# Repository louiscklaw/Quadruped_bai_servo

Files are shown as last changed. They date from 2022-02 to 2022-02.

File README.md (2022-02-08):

# Quadruped_bai_servo v1
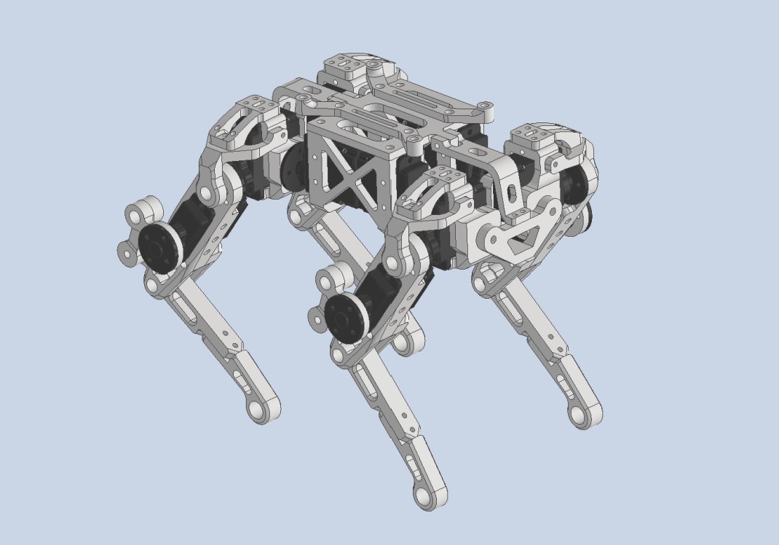
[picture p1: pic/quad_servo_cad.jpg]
quad_servo_cad


A low cost 12DOF quadruped, actuated by hobby servos. Notice that this is an early version developed back in 2019. If you're looking for a high performance desktop quad, check out the ongoing [Quadruped bai tiny](https://github.com/psrobotics/Quadruped_bai_tiny)

This repository contains the models, BOM, electronic, simulate, as well as the source code of the project.

## Videos

[Balancing](https://www.youtube.com/watch?v=fsc0w1NeIVk)

[Walking](https://youtu.be/FCRvykWv6ok)

## Hardware

Required parts are listed below. For all printed parts, the recommended printing infill is 70%. Set up proper printing direction and support based on your printer type.

| Part Name | Quantity | Link | Info |
| --- | --- | --- | --- |
| leg_tip | 2 | [STL file](hardware/stl) | Printed part |
| leg_tip_MIR | 2 | / | / |
| leg_2 | 2 | / | / |
| leg_2_MIR | 2 | / | / |
| leg_link_1 | 2 | / | / |
| leg_link_1_MIR | 2 | / | / |
| leg_link-1 | 2 | / | / |
| leg_link-1_MIR | 2 | / | / |
| leg_1 | 2 | / | / |
| leg_1_MIR | 2 | / | / |
| leg_1_2 | 2 | / | / |
| leg_1_2_MIR | 2 | / | / |
| servo_holder_1 | 2 | / | / |
| servo_holder_1_MIR | 2 | / | / |
| hip_joint_holder_1 | 2 | / | / |
| hip_joint_holder_1_MIR | 2 | / | / |
| hip_holder_2 | 2 | / | / |
| hip_holder_2_MIR | 2 | / | / |
| joint_ab_holder | 2 | / | / |
| body_bridge | 2 | / | / |
| body_frame_2 | 1 | / | / |
| body_frame_1 | 1 | / | / |
| pcb_holder | 2 | / | / |
| M3*8 | ~20 | / | Screw |
| M3*12 | ~30 | / | / |
| M3*16 | ~20 | / | / |
| M2*8 | ~50 | / | / |
| M2*15 | ~50 | / | / |
| M2*20 | ~20 | / | / |
| M2*26 | ~20 | / | / |
| SF-1 0305 Self Lubricating Composite Bearing Bushing Sleeve | ~25 | [ebay](https://www.ebay.com/itm/141882850401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) | For rotation joints |
| EMAX ES08A II Servo | 12 | [EMAX](https://emaxmodel.com/products/emax-es08a-ii-mini-plastic-gear-analog-servo-1-8kg-sec-for-rc-models-robot) | Actuator |

After printing your parts, insert the bearing at all 5mm holes locates around rotations joints. Then fasten  parts with M3 screws. Remember to check the rotation friction, make sure all joints can rotates freely with the servo installed. 

### Servo selection

The performance of actuators is of fundamental importance for legged robots. Even when we're building a small one. Ideal actuators for this design should be highly back-drivable, have high power density, and be torque-controllable. However, most off-the-shelf servos have nothing to do with these features. There are some high voltage brushless servos (with magnetic encoders for feedback) with relatively good performance, but they're extremely costive at this size. If you have enough budget, why not build a brushless one? Considering that you'll need 12 servos for the assembly, my suggestion is just to go for the budget choice. The EMAX ES08A (metal gear version) works fine for my build. The nylon gear version is also acceptable, but they can easily be damaged under impact.

### Body assembly

The robot consists 4 legs and a body frame. Assembly 2 legs first.

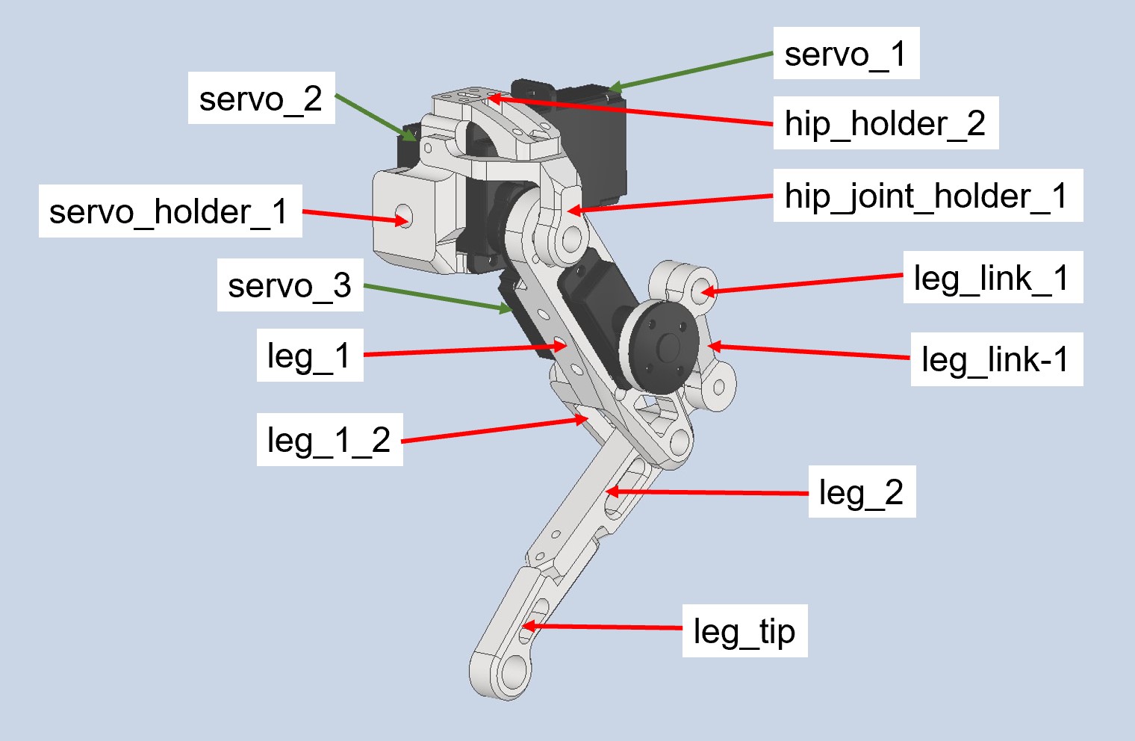
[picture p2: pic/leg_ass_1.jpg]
leg_ass_1


Assembly another 2 mirrored legs. Then link all legs to the body frame.

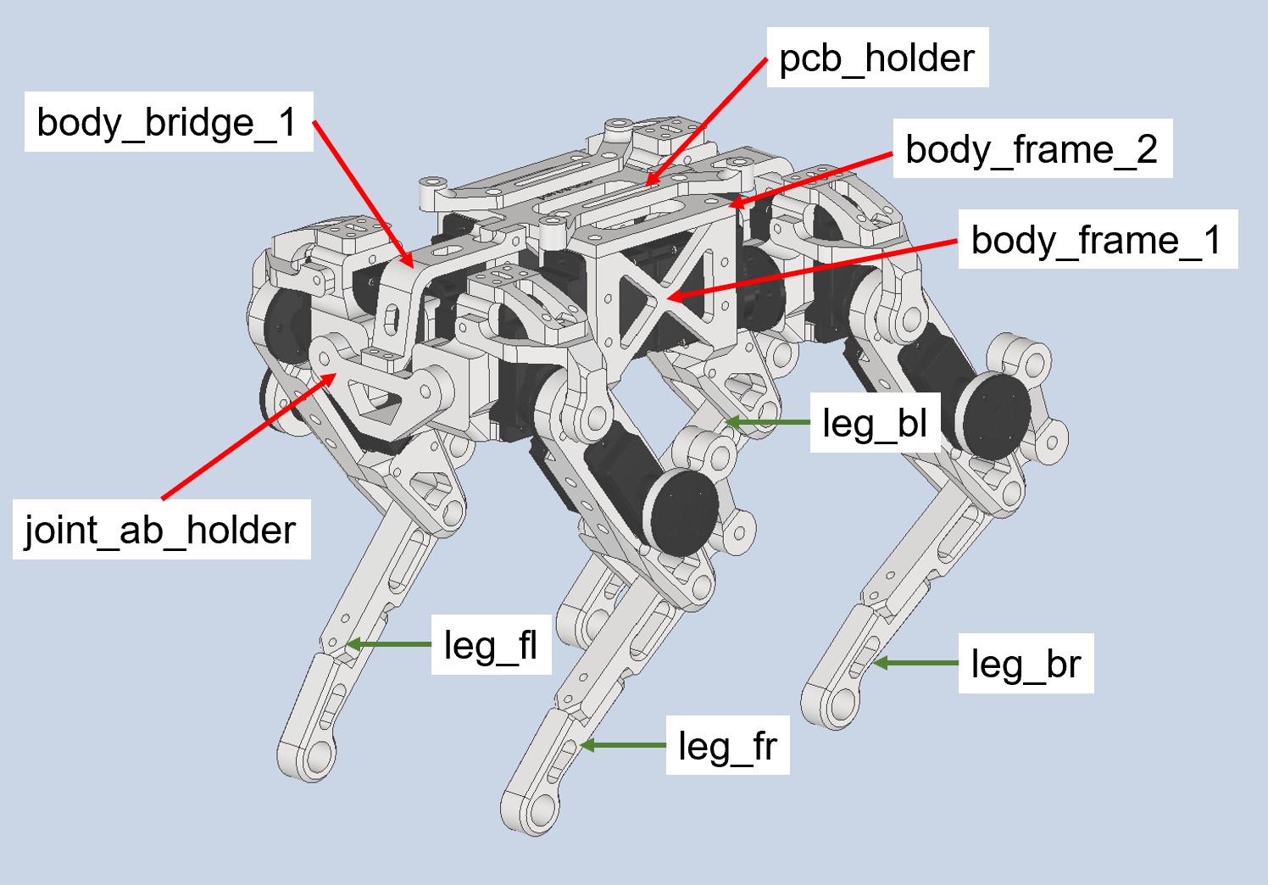
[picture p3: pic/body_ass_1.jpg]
body_ass_1


### Feet Sensor (optional)

Additional feet sensors can detect whether foot have touched the ground. This can be helpful when changing the state machine from 'swing state' to 'stance state'. The foot of Quadruped bai servo is switchable. If you decided to add feet sensors, some additional configurations are needed for the firmware (would be detailly explained later). 

Feet sensors are built around micro switches,  which detect impact from specific directions. As for the result, this design didn't work that well. A good feet sensor solution should be able to detect impacts from all directions, with low latency and clear output. [Open Dynamic Robot Initiative](https://open-dynamic-robot-initiative.github.io/) has presented an elegant solution with infrared sensor. Take that as a reference, the ongoing Quadruped bai tiny will come with better feet sensors. Assembly the feet sensor as this pic shown. (Remember to print mirrored parts for right-side legs)

Only 3 printed parts are needed to assembly the feet sensor, check [STL file](hardware/stl/feet_sensor) here.

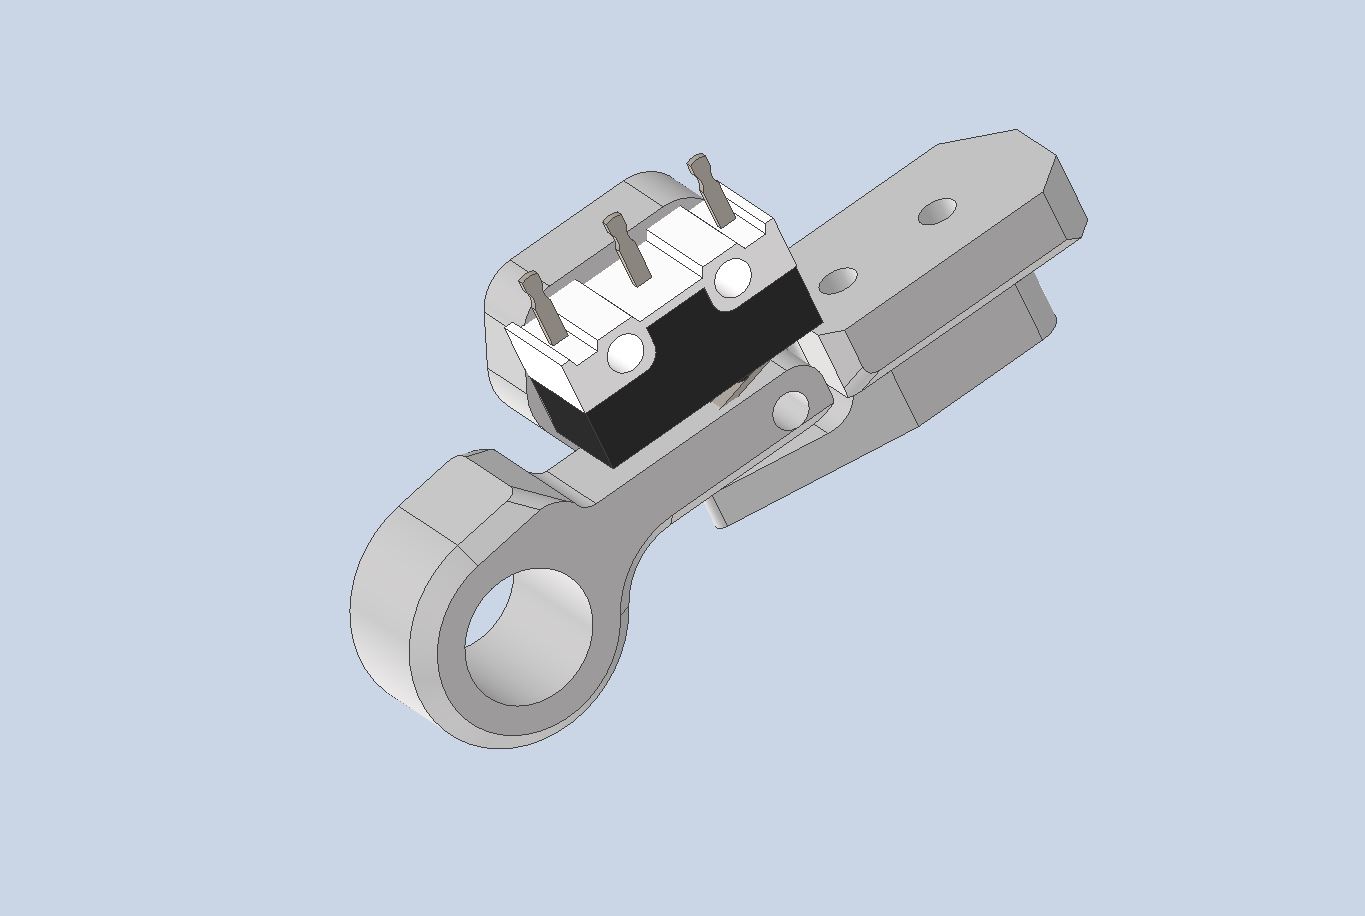
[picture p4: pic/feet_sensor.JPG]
feet_sensor


In order to increase the friction between feet and ground, additional high-friction coating is vital. I used some glued silicone sheet on the feet tip. You can also design your feet tip and print it with high-friction material.

### Servo Calibration

Most servos have a limited motion range,  make sure the servo's motion range covers leg linkage's joint limit shown in the following pics.  Also, pre-calibrate in this step by applying an initial PWM signal to servos before installing (eg. 0°). This enables all servos to have the same PWM-joint angle mapping. You can then fine-tuning them in the firmware.

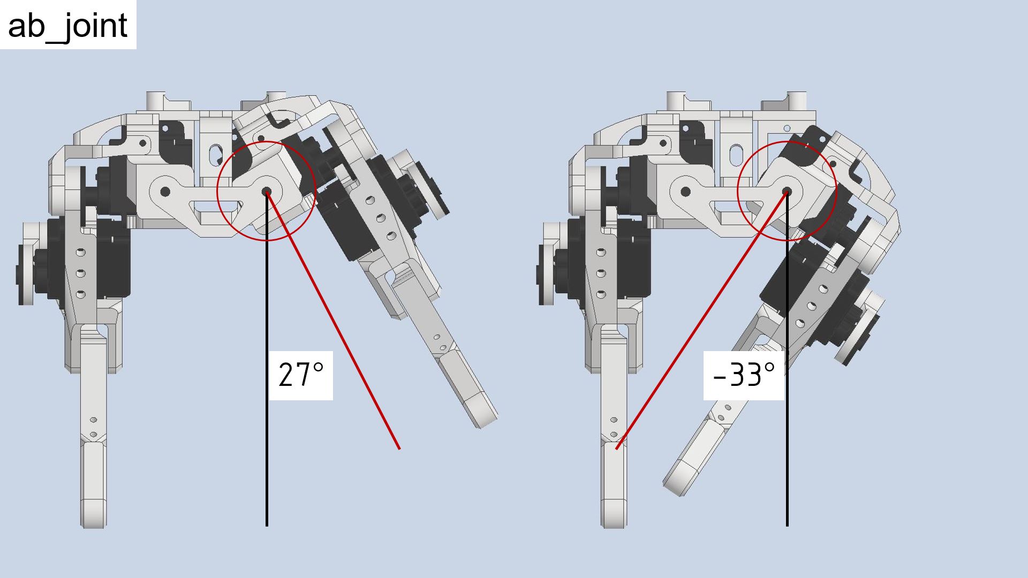
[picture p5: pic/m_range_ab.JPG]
ab joint


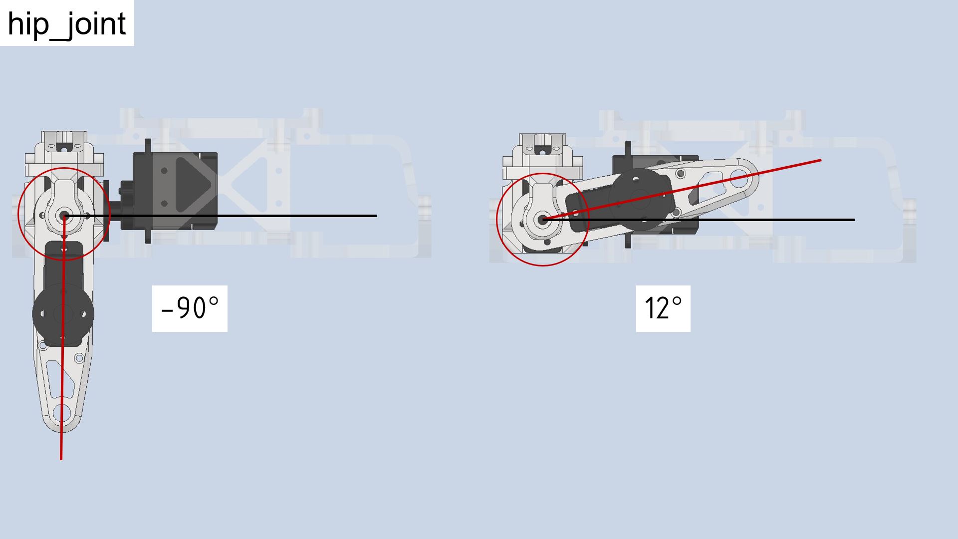
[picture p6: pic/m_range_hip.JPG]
hip joint


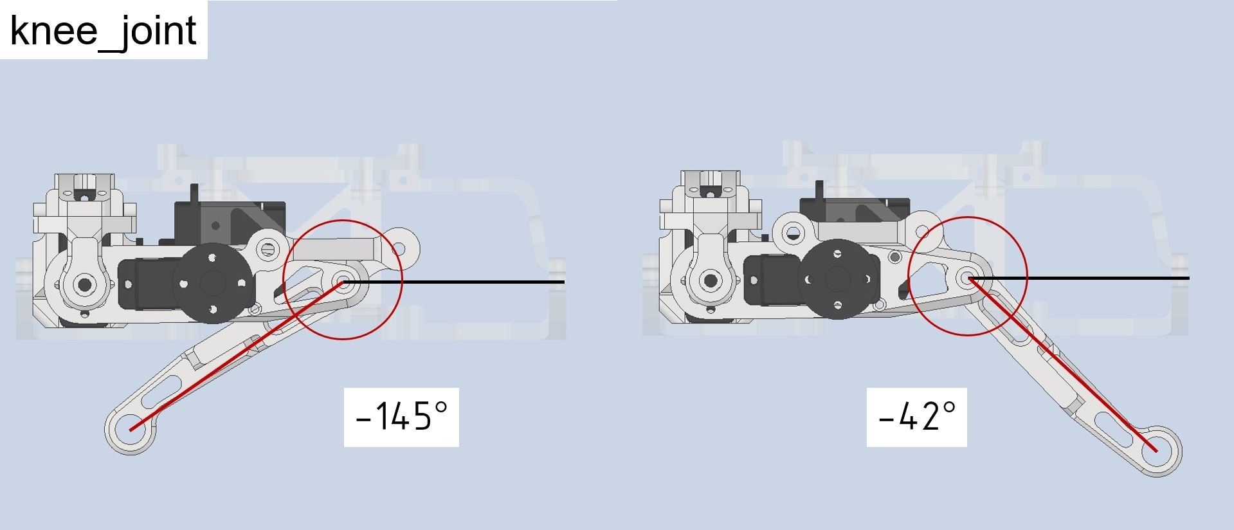
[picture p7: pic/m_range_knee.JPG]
knee joint


## Electronic

The controller board assembly includes servo controller, IMU, and dc-dc converter module. With an additional serial port, you can connect robot to a wireless or Bluetooth module that enables wireless control. Built around ATmega328P, the microcontroller's performance, IO is just not enough for such application. I encourage you take this schematic as a reference and switch to a high performance 32-bit microcontroller (something like STM32H7, ESP32). If you're more comfortable with AVR Arduino boards, use this design directly and it'll work.

[PCBs](electronic/) are designed with [EAGLE](https://www.autodesk.com/products/eagle/free-download). Exported Gerber file is uploaded too. If you don't want to order the PCB, you can also make it using off-the-shelf components (Arduino nano, MPU 6050, dc-dc converter, etc).

### Controller board pin assignment

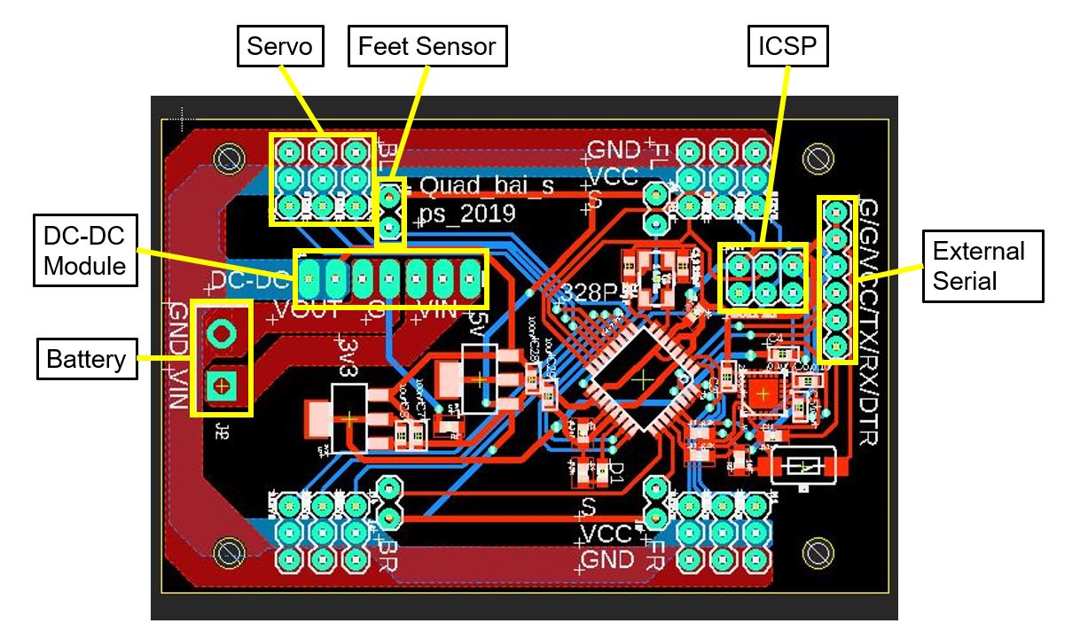
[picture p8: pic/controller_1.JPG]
ctr_brd


Use ICSP to upload firmware and debug with the external serial port. The hardware IIC pins(A4,A5) are occupied by IMU (MPU6050 is also an 'old chip', you can replace with something like BNO080). 

### DC-DC converter

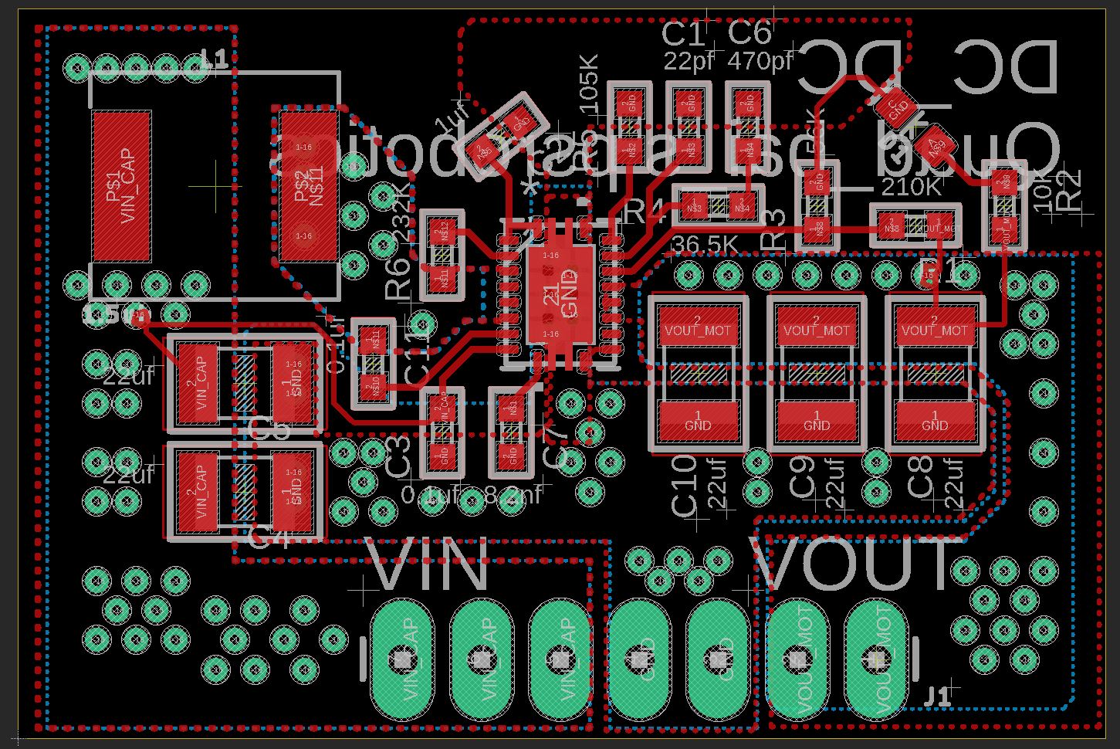
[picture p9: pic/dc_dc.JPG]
dc_dc


Integrated boost converter to power servos. Pre-configured output voltage is 5.5V, you can change by [replacing](https://www.ti.com/lit/ds/symlink/tps61088.pdf?ts=1644121246192#:~:text=The%20TPS61088%20is%20a%20high,size%20solution%20in%20portable%20systems.&text=The%20device%20has%2010%2DA,voltage%20up%20to%2012.6%20V.) the feedback resistor. Plug this module to the DC-DC slot on controller board.

### Battery

Single-cell lithium batteries with high current output capability(>10A) are preferred. This project uses 18650, 18350 batteries. The [battery shelf](hardware/step) can be printed and mounted under the robot frame.

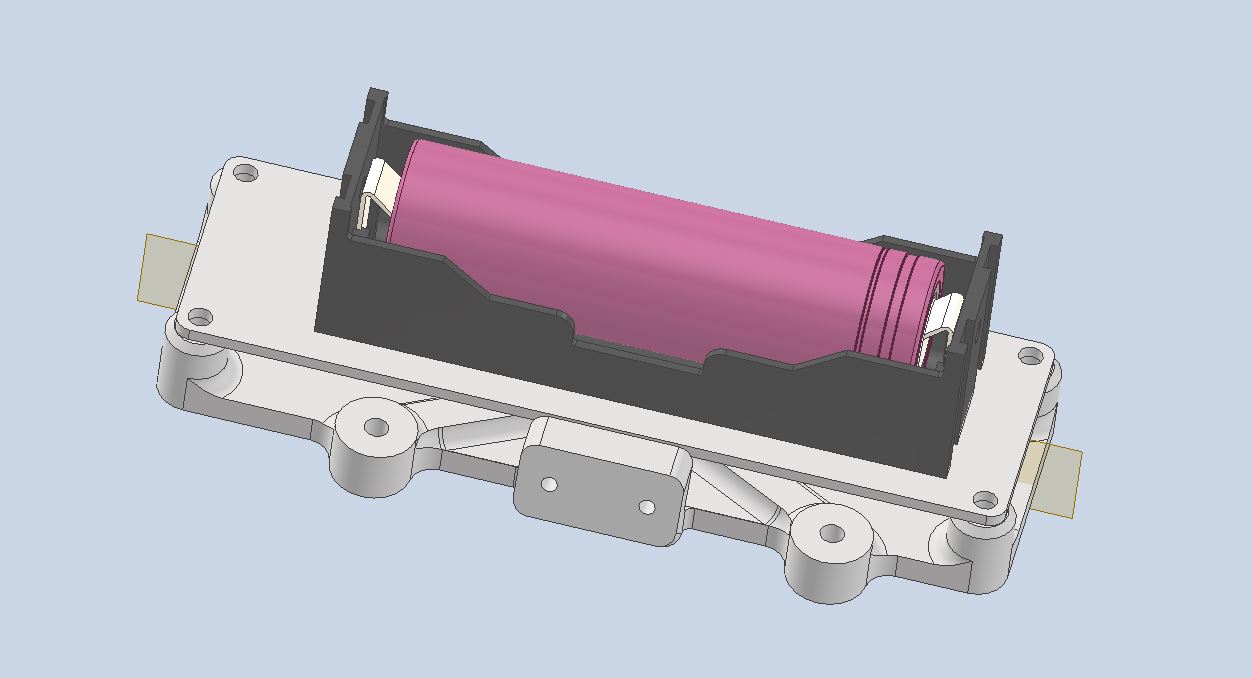
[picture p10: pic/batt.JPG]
batt


## Simulate

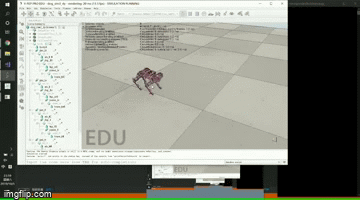
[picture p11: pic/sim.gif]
simulate


Simplified model in [v-rep](https://www.coppeliarobotics.com/). You can use remote API to develop your simulation.

### Coordinate system in the simulation

TODO, write this docu when I'm free.

## Firmware

A simplified controller is implemented to generate trot pattern for walking. Here, I applied a state machine to easily synchronize a set of open foot trajectories (with feet sensor). The IMU unit is used to adjust body roll&pitch during the stance phase. Notice that this robot is only controlled on the kinematic level, don't expect it to resist external impacts during walking process.

## License

Under BSD-3-Clause license, COME WITH NO WARRANTIES, BUILD AT YOUR RISK.

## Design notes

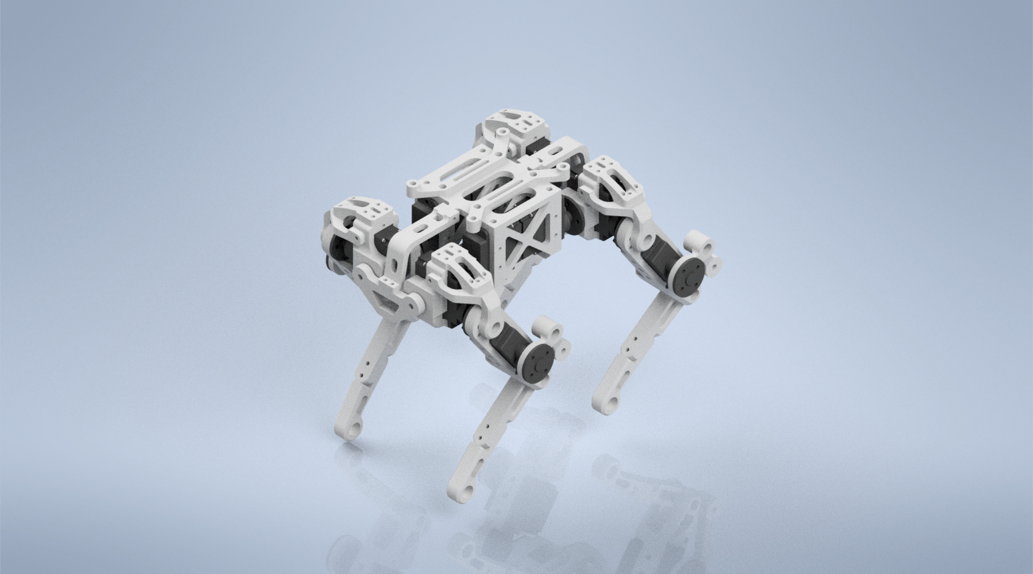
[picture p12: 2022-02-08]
docs/index.png

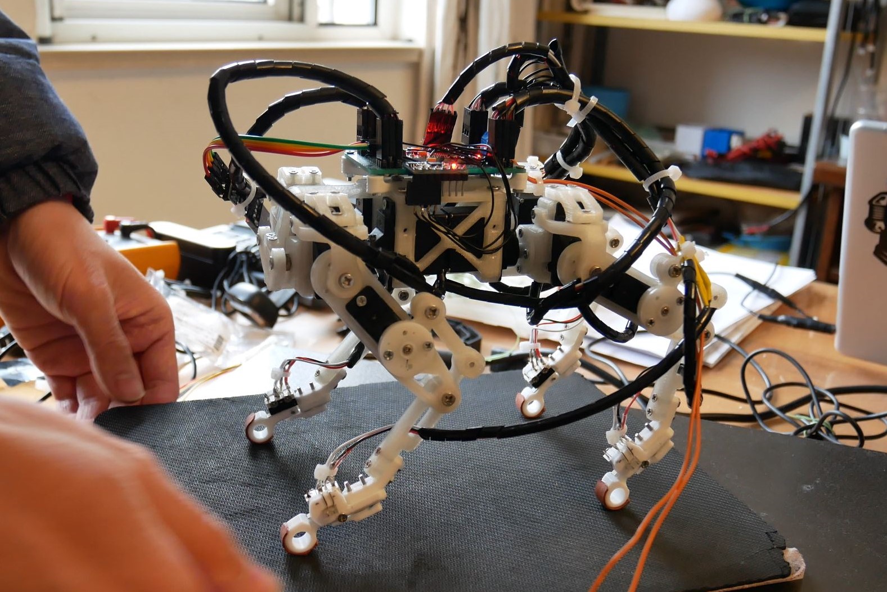
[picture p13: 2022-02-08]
pic/quad_servo.jpg

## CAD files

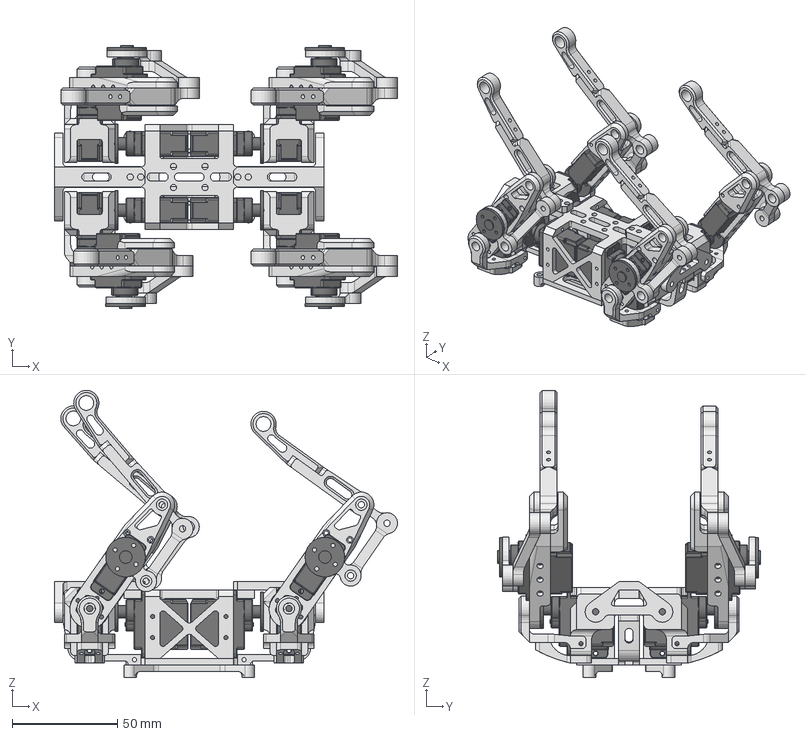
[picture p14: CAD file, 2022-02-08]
hardware/step/quadruped_bai_servo_assembly.stp
162.6 x 124.6 x 136.2 mm
Emax ES08A x 6
leg_1 x 2
leg_2 x 2
leg_1_2 x 2
leg_link_1 x 2
leg_link-1 x 2
leg_tip x 2
servo_holder_1
hip_joint_holder_1 x 2
hip_holder_2 x 2
servo_holder_1_MIR
Emax ES08A_MIR x 6
leg_1_MIR x 2
leg_2_MIR x 2
leg_1_2_MIR x 2
leg_link_1_MIR x 2
leg_link-1_MIR x 2
leg_tip_MIR x 2
servo_holder_1_MIR1
hip_joint_holder_1_MIR x 2
hip_holder_2_MIR x 2
servo_holder_1_MIR_MIR
body_frame_1
joint_ab_holder x 2
body_frame_2
body_bridge_1 x 2
pcb_holder x 2

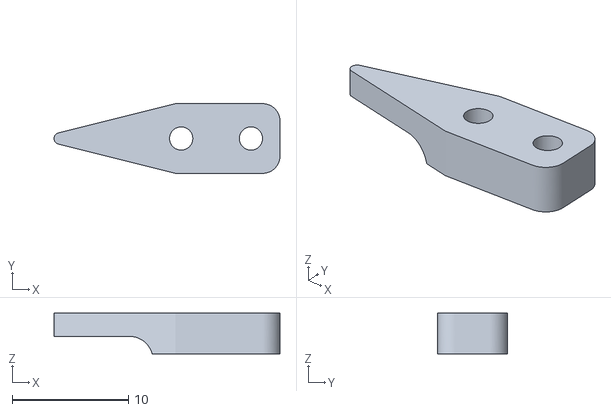
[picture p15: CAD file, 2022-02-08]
hardware/stl/feet_sensor/sensor_shelf.stl
19.4 x 6.00 x 3.50

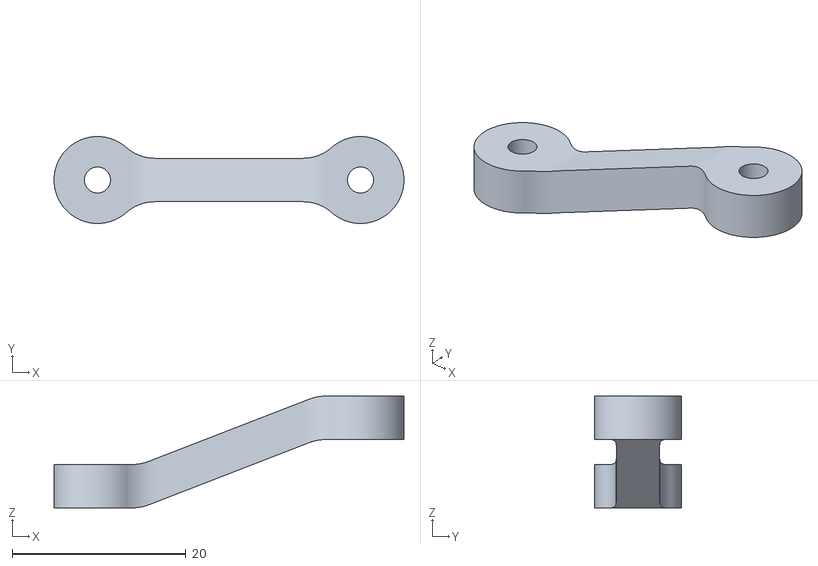
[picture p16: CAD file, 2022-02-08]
hardware/stl/leg_link-1.stl
40.2 x 10.00 x 12.9

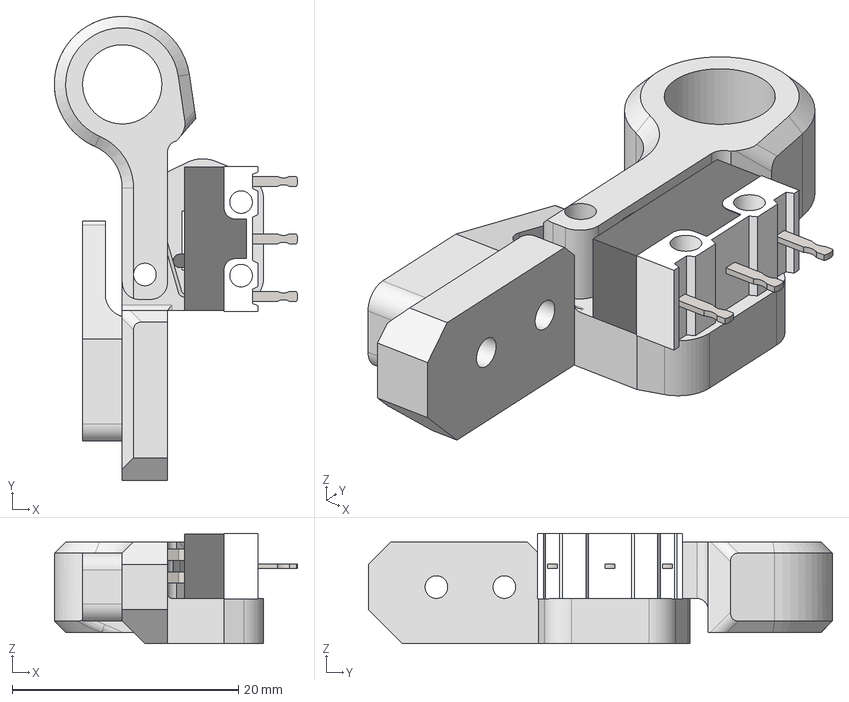
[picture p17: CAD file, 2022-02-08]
hardware/step/feet_sensor.stp
21.5 x 41.0 x 9.75 mm
leg_tip
D2F-01L
leg_tip_1
sensor_shelf

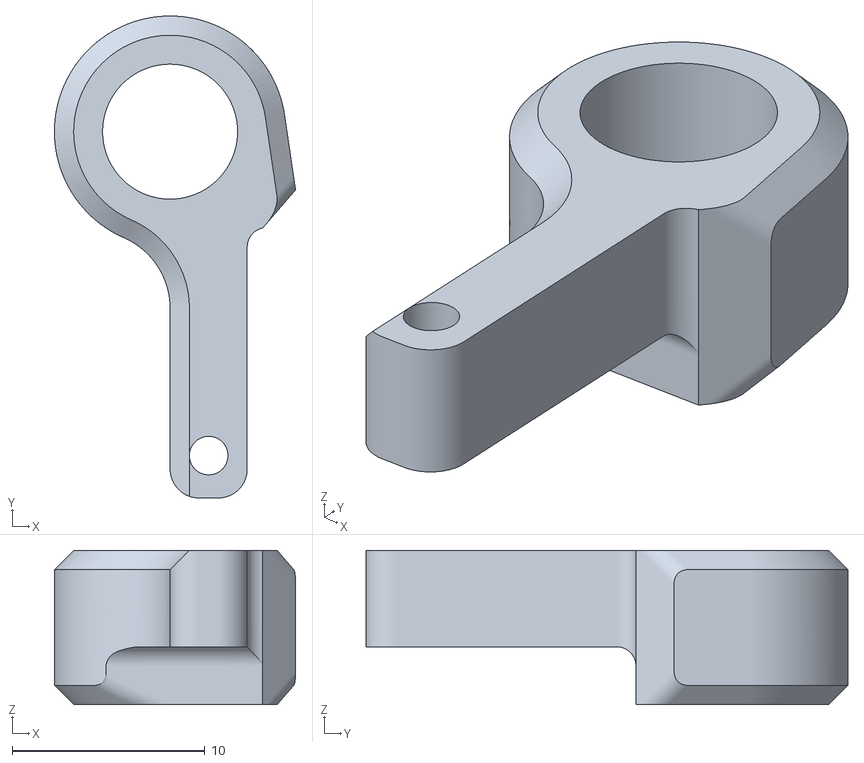
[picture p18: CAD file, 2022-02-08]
hardware/stl/feet_sensor/leg_tip_sensor2.stl
12.5 x 25.0 x 8.00

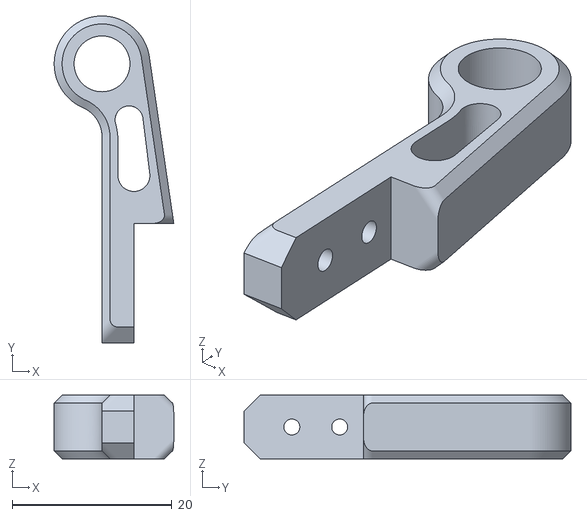
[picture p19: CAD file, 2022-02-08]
hardware/stl/leg_tip_MIR.stl
15.0 x 41.0 x 8.00

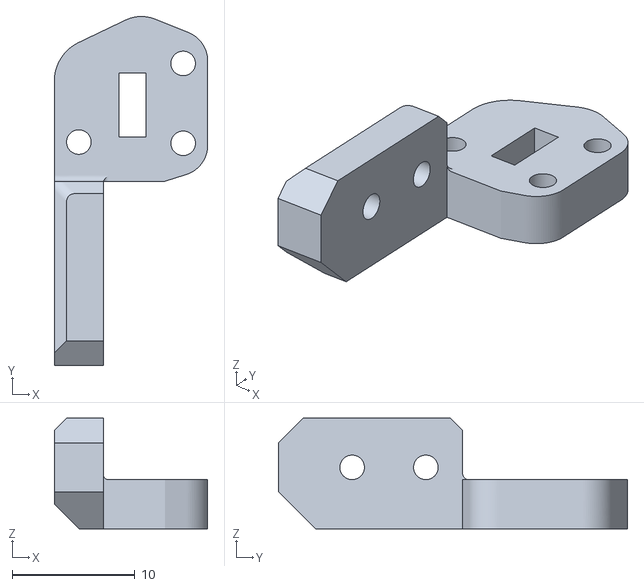
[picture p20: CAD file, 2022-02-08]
hardware/stl/feet_sensor/leg_tip_sensor.stl
12.5 x 28.4 x 9.00

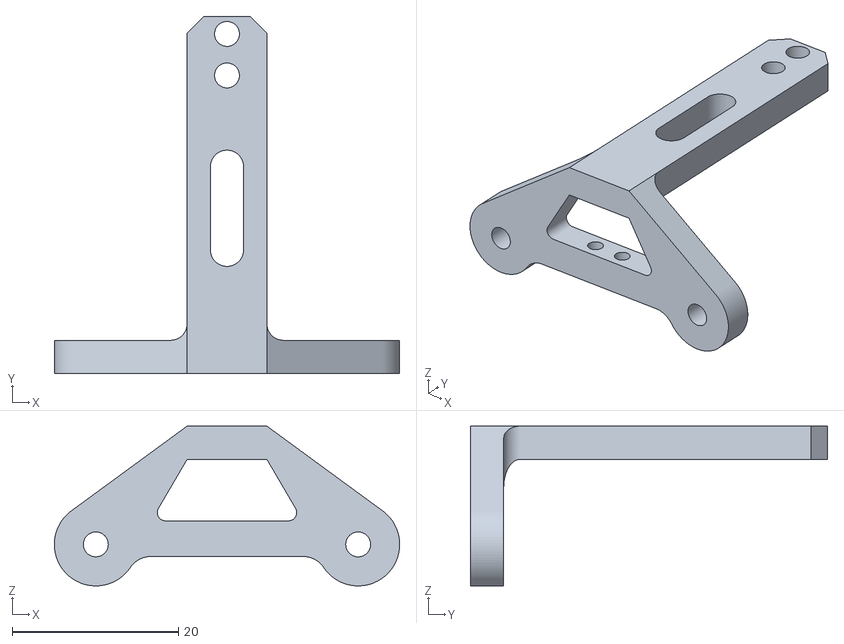
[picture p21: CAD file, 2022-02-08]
hardware/stl/joint_ab_holder.stl
41.6 x 43.0 x 19.2

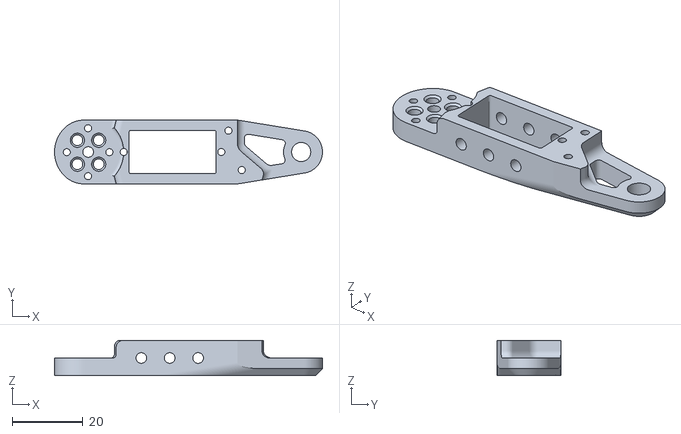
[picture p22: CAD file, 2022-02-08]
hardware/stl/leg_1.stl
75.5 x 18.0 x 10.0

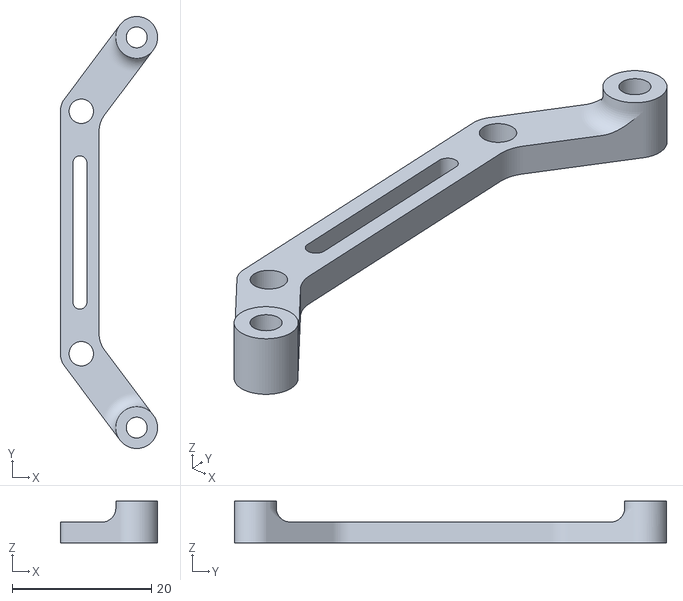
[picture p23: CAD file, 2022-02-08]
hardware/stl/pcb_holder.stl
13.9 x 62.0 x 6.00

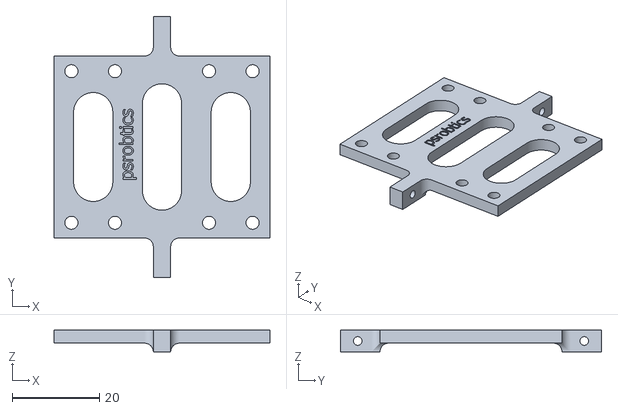
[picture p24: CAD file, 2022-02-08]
hardware/stl/body_frame_2.stl
49.6 x 60.0 x 5.00

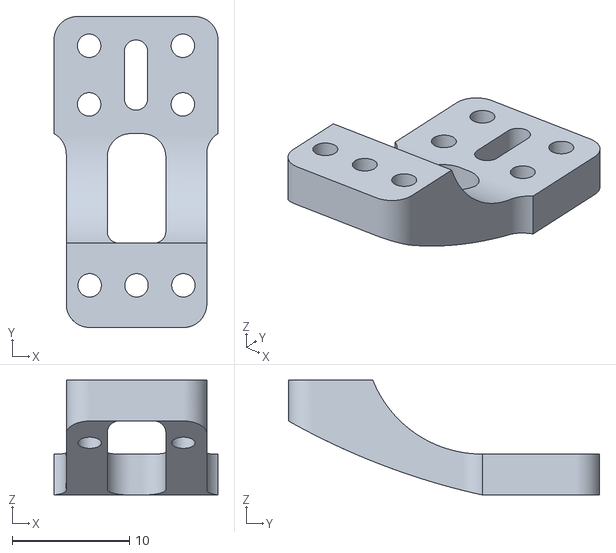
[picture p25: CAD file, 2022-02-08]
hardware/stl/hip_holder_2_MIR.stl
14.0 x 26.5 x 9.82

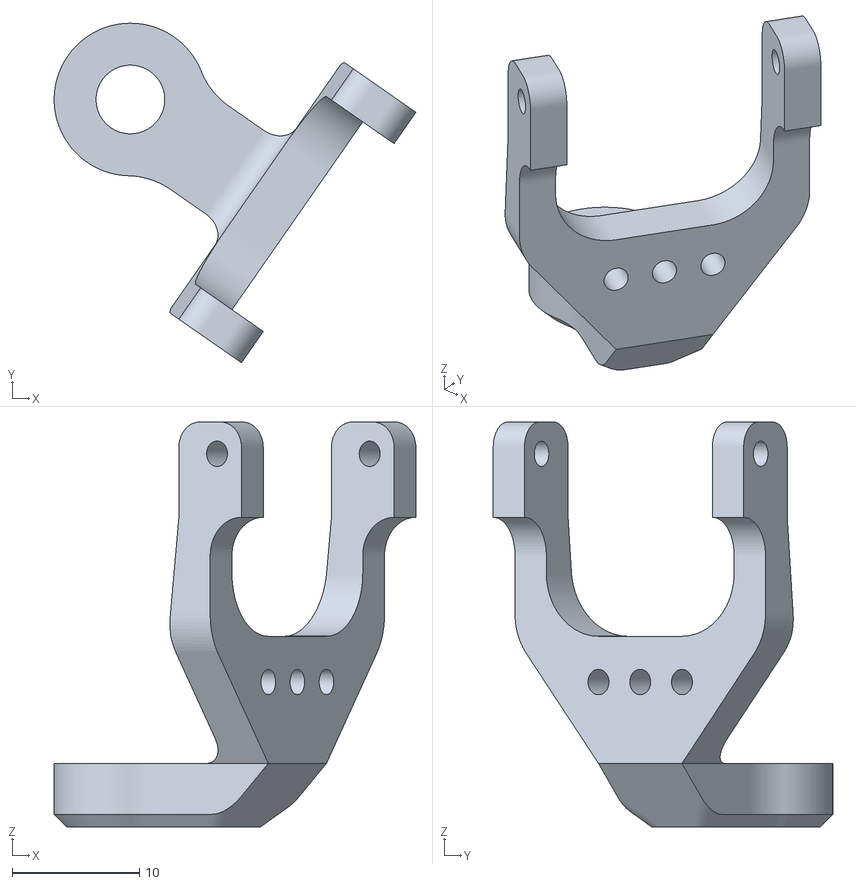
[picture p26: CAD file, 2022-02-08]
hardware/stl/hip_joint_holder_1_MIR.stl
28.4 x 26.7 x 31.9

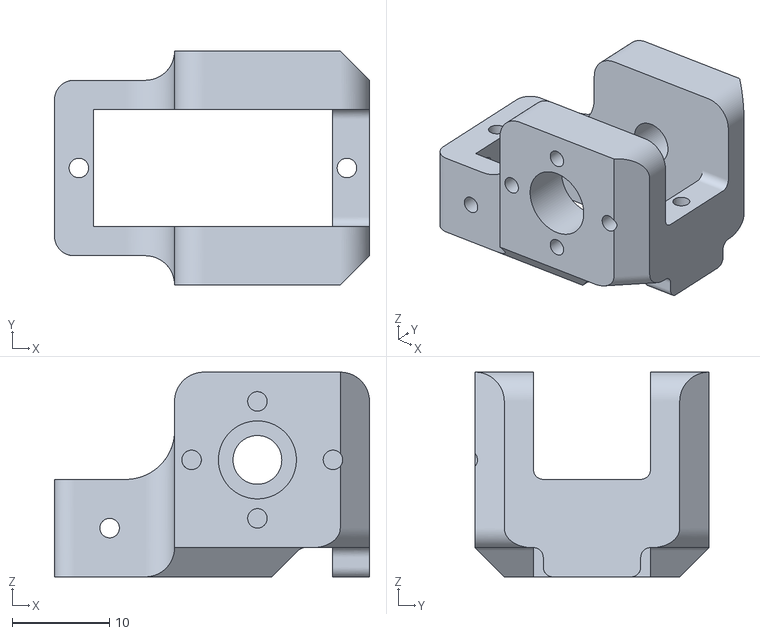
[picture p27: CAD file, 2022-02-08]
hardware/stl/servo_holder_1.stl
32.3 x 24.0 x 21.0

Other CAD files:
hardware/stl/leg_1_MIR.stl
hardware/stl/leg_tip.stl
hardware/stl/hip_joint_holder_1.stl
hardware/stl/body_frame_1.stl
hardware/inventor/18650_battery_pack/18650_bat.ipt
hardware/inventor/18650_battery_pack/18650_battery_pack.iam
hardware/inventor/18650_battery_pack/18650_pack.iam
hardware/inventor/18650_battery_pack/Li-Ion_Cell_Holder_BH_18650_A.ipt
hardware/inventor/18650_battery_pack/Samsung 30Q 18650 Battery.ipt
hardware/inventor/18650_battery_pack/ele_holder_1.ipt
hardware/inventor/feet_sensor/D2F-01L.ipt
hardware/inventor/feet_sensor/feet_sensor.iam
hardware/inventor/feet_sensor/leg_tip_sensor.ipt
hardware/inventor/feet_sensor/leg_tip_sensor2.ipt
hardware/inventor/feet_sensor/sensor_shelf.ipt
hardware/inventor/quadruped_bai_servo_assembly/Emax ES08A.ipt
hardware/inventor/quadruped_bai_servo_assembly/Emax ES08A_MIR.ipt
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

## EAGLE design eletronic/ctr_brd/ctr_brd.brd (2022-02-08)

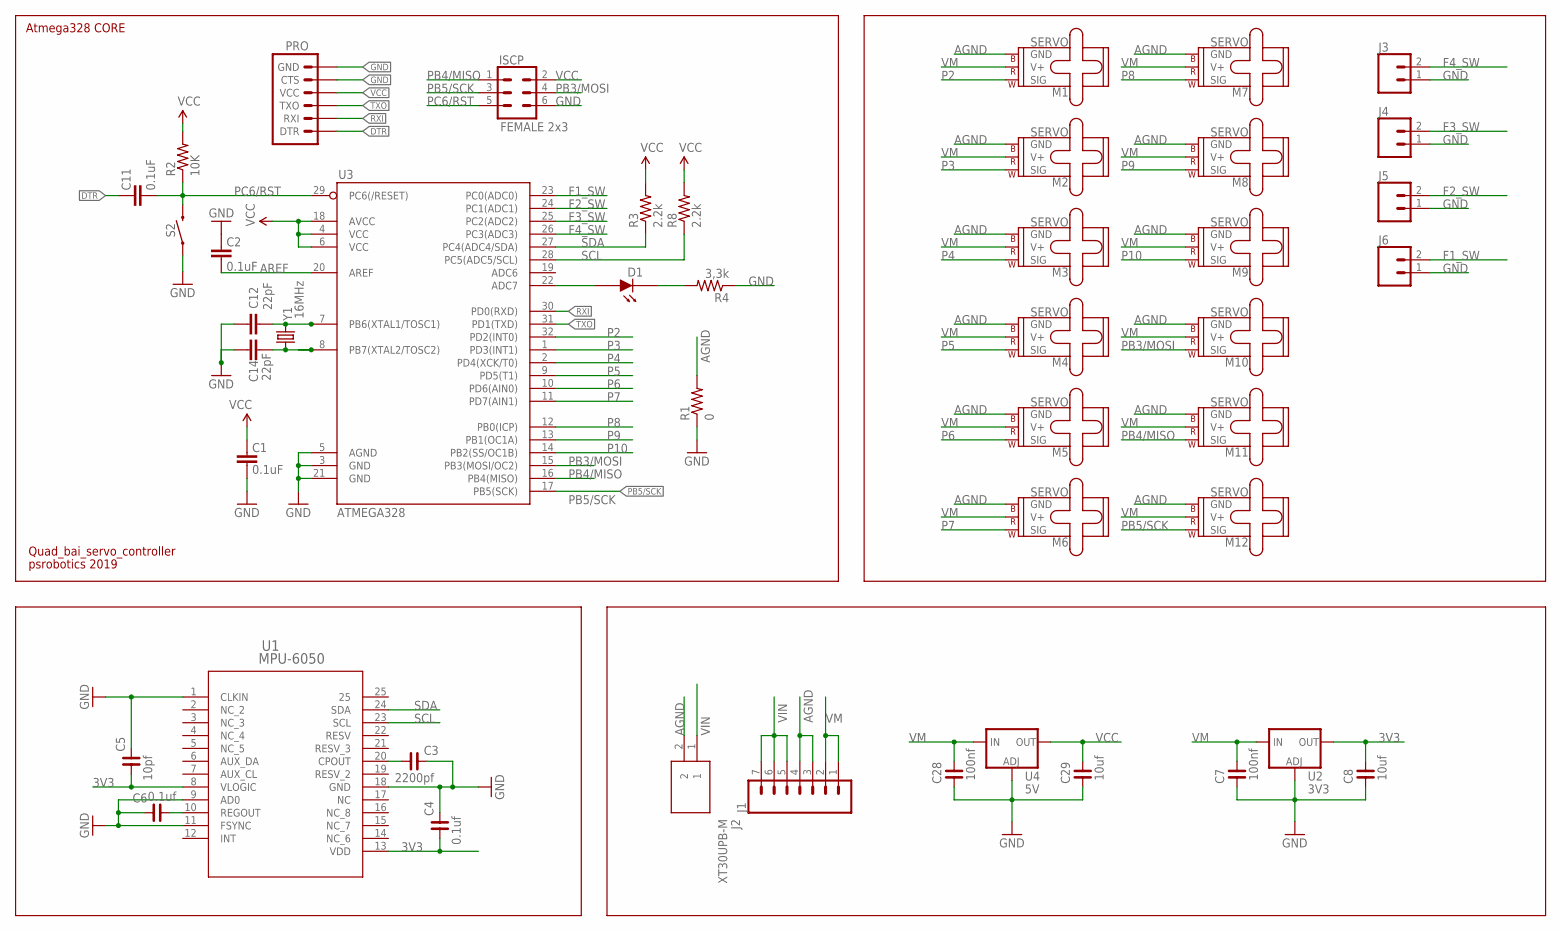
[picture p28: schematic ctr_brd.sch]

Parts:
C1, C2, C11: 0.1uF; 0603-CAP
C3: 2200pf; C0603
C4, C6: 0.1uf; C0603
C5: 10pf; C0603
C7, C28: 100nf; C0603
C8, C29: 10uf; C0603
C12, C14: 22pF; 0603
D1: LEDB; 0603P
ISCP: FEMALE 2x3; 2X3
J1: CONN_07LONGPADS; 1X07_LONGPADS
J2: XT30UPB-M; SHDR2W160P0X500_1X2_1020X520X1
J3, J4, J5, J6: CONN_02LOCK; 1X02_LOCK
M1, M2, M3, M4, M5, M6, M7, M8, M9, M10, M11, M12: SERVO; 1X03
PRO: FTDI Basic; 1X06
R1: 0; 0603-RES
R2: 10K; 0603-RES
R3, R8: 2.2k; 0603-RES
R4: 3,3k; 0603-RES
S2: MOMENTARY-SWITCH-SPST-SMD-6.0X3.5MM; TACTILE_SWITCH_SMD_6.0X3.5MM
U1: MPU-6050; QFN24_4X4X0P9_IVS
U2: 3V3; SOT223
U3: ATMEGA328; TQFP32-08
U4: 5V; SOT223
Y1: 16MHz; CRYSTAL-SMD-5X3.2-4PAD

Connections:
3V3: C4.1, C5.1, C8.2, U1.8 (VLOGIC), U1.13 (VDD), U2.2 (OUT), U2.4 (OUT)
AGND: J1.3, J1.4, J2.2, M1.3 (GND), M2.3 (GND), M3.3 (GND), M4.3 (GND), M5.3 (GND), M6.3 (GND), M7.3 (GND), M8.3 (GND), M9.3 (GND), M10.3 (GND), M11.3 (GND), M12.3 (GND), R1.2
AREF: C2.1, U3.20 (AREF)
DTR: C11.2, PRO.1 (DTR)
F1_SW: J6.2, U3.23 (PC0(ADC0))
F2_SW: J5.2, U3.24 (PC1(ADC1))
F3_SW: J4.2, U3.25 (PC2(ADC2))
F4_SW: J3.2, U3.26 (PC3(ADC3))
GND: C1.1, C2.2, C3.2, C4.2, C5.2, C6.2, C7.1, C8.1, C12.1, C14.1, C28.1, C29.1, ISCP.6, J3.1, J4.1, J5.1, J6.1, PRO.5 (CTS), PRO.6 (GND), R1.1, R4.1, S2.1, U1.1 (CLKIN), U1.9 (AD0), U1.11 (FSYNC), U1.18 (GND), U2.1 (ADJ), U3.3 (GND), U3.5 (AGND), U3.21 (GND), U4.1 (ADJ)
unnamed: C14.2, U3.8 (PB7(XTAL2/TOSC2)), Y1.1
unnamed: C12.2, U3.7 (PB6(XTAL1/TOSC1)), Y1.3 (2)
unnamed: C3.1, U1.20 (CPOUT)
unnamed: C6.1, U1.10 (REGOUT)
unnamed: D1.1 (D_IN), U3.22 (ADC7)
unnamed: D1.2 (D_OUT), R4.2
P2: M1.1 (SIG), U3.32 (PD2(INT0))
P3: M2.1 (SIG), U3.1 (PD3(INT1))
P4: M3.1 (SIG), U3.2 (PD4(XCK/T0))
P5: M4.1 (SIG), U3.9 (PD5(T1))
P6: M5.1 (SIG), U3.10 (PD6(AIN0))
P7: M6.1 (SIG), U3.11 (PD7(AIN1))
P8: M7.1 (SIG), U3.12 (PB0(ICP))
P9: M8.1 (SIG), U3.13 (PB1(OC1A))
P10: M9.1 (SIG), U3.14 (PB2(SS/OC1B))
PB3/MOSI: ISCP.4, M10.1 (SIG), U3.15 (PB3(MOSI/OC2))
PB4/MISO: ISCP.1, M11.1 (SIG), U3.16 (PB4(MISO))
PB5/SCK: ISCP.3, M12.1 (SIG), U3.17 (PB5(SCK))
PC6/RST: C11.1, ISCP.5, R2.1, S2.2, U3.29 (PC6(/RESET))
RXI: PRO.2 (RXI), U3.30 (PD0(RXD))
SCL: R8.1, U1.23 (SCL), U3.28 (PC5(ADC5/SCL))
SDA: R3.1, U1.24 (SDA), U3.27 (PC4(ADC4/SDA))
TXO: PRO.3 (TXO), U3.31 (PD1(TXD))
VCC: C1.2, C29.2, ISCP.2, PRO.4 (VCC), R2.2, R3.2, R8.2, U3.4 (VCC), U3.6 (VCC), U3.18 (AVCC), U4.2 (OUT), U4.4 (OUT)
VIN: J1.5, J1.6, J1.7, J2.1
VM: C7.2, C28.2, J1.1, J1.2, M1.2 (V+), M2.2 (V+), M3.2 (V+), M4.2 (V+), M5.2 (V+), M6.2 (V+), M7.2 (V+), M8.2 (V+), M9.2 (V+), M10.2 (V+), M11.2 (V+), M12.2 (V+), U2.3 (IN), U4.3 (IN)

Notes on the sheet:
Atmega328 CORE
Quad_bai_servo_controller
psrobotics 2019

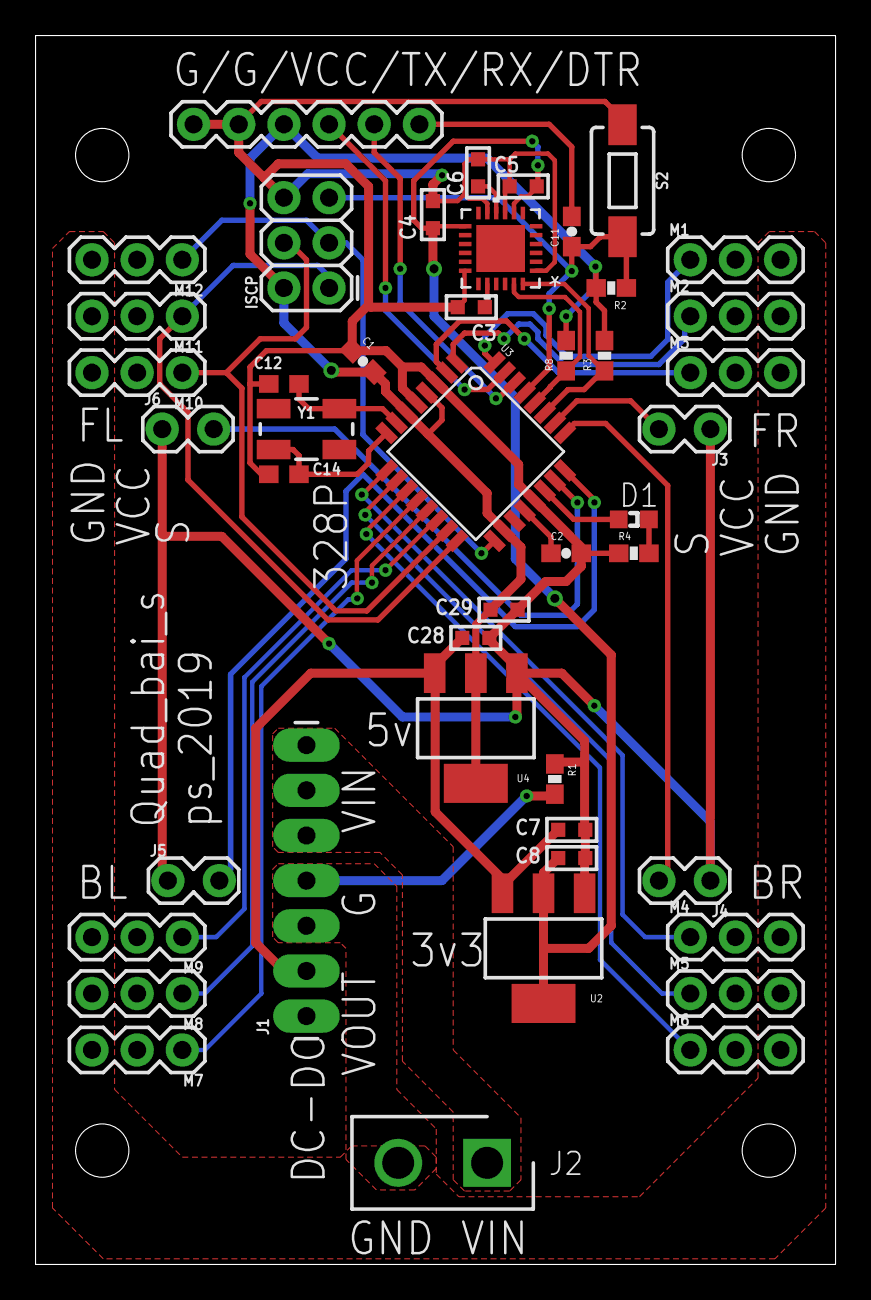
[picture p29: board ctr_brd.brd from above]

Board: 2 copper layers, 45.0 x 69.1 mm, 45 parts (0 on the bottom side), 35 nets.

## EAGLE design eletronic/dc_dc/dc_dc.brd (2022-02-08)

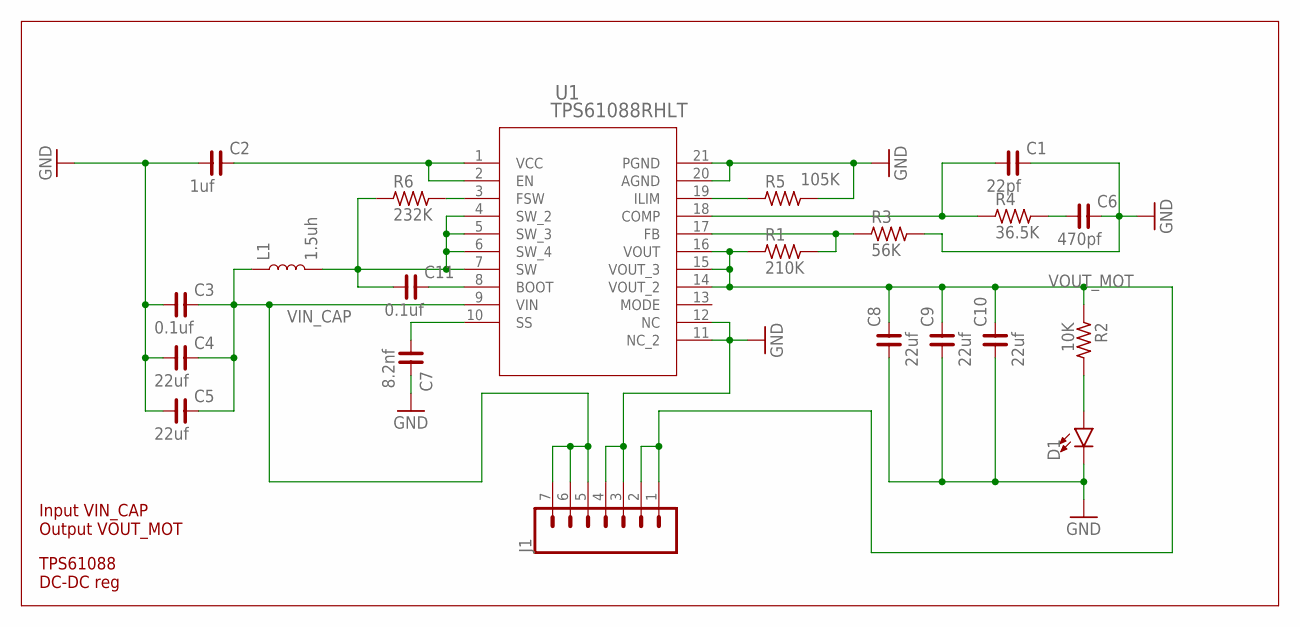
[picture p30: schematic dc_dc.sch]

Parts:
C1: 22pf; C0603
C2: 1uf; C0603
C3, C11: 0.1uf; C0603
C4, C5, C8, C9, C10: 22uf; C1210
C6: 470pf; C0603
C7: 8.2nf; C0603
D1: LED0603; LED-0603
J1: CONN_07LONGPADS; 1X07_LONGPADS
L1: 1.5uh; CR75
R1: 210K; R0603
R2: 10K; R0603
R3: 56K; R0603
R4: 36.5K; R0603
R5: 105K; R0603
R6: 232K; R0603
U1: TPS61088RHLT; RHL0020A_TEX

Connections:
GND: C1.2, C2.1, C3.1, C4.1, C5.1, C6.2, C7.2, C8.1, C9.1, C10.1, D1.C, J1.3, J1.4, R3.2, R5.2, U1.11 (NC_2), U1.12 (NC), U1.20 (AGND), U1.21 (PGND)
unnamed: C7.1, U1.10 (SS)
unnamed: R5.1, U1.19 (ILIM)
unnamed: C1.1, R4.1, U1.18 (COMP)
unnamed: C6.1, R4.2
unnamed: C2.2, U1.1 (VCC), U1.2 (EN)
unnamed: R1.2, R3.1, U1.17 (FB)
unnamed: D1.A, R2.2
unnamed: C11.2, U1.8 (BOOT)
unnamed: C11.1, L1.P$2 (2), R6.1, U1.4 (SW_2), U1.5 (SW_3), U1.6 (SW_4), U1.7 (SW)
unnamed: R6.2, U1.3 (FSW)
VIN_CAP: C3.2, C4.2, C5.2, J1.5, J1.6, J1.7, L1.P$1 (1), U1.9 (VIN)
VOUT_MOT: C8.2, C9.2, C10.2, J1.1, J1.2, R1.1, R2.1, U1.14 (VOUT_2), U1.15 (VOUT_3), U1.16 (VOUT)

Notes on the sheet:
TPS61088 DC-DC reg
Input VIN_CAP Output VOUT_MOT

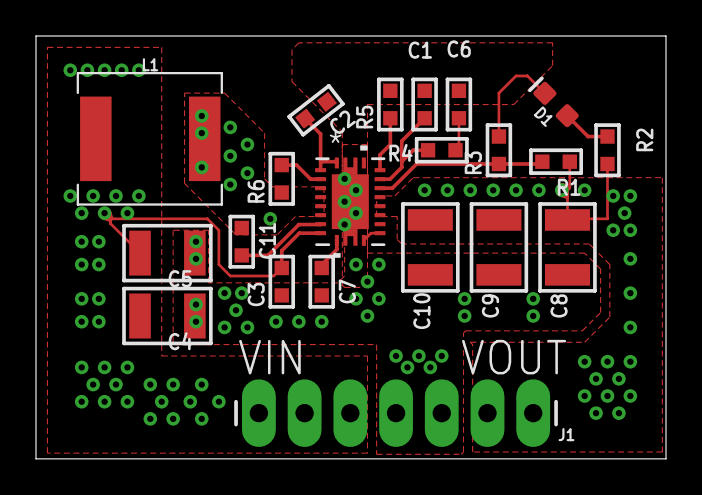
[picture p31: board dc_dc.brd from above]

Board: 2 copper layers, 35.0 x 23.5 mm, 21 parts (0 on the bottom side), 13 nets.

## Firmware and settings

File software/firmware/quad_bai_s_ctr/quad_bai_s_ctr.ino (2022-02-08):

//Quad controller for atmega328p
//Shuang Peng - 2019-02 ver0.2

#include "matrix.h"
#include "kinematics.h"
#include "gait_generator.h"
#include "mpu_sensor.h"
#include <Servo.h>
#include <FlexiTimer2.h>

#define steady_pos_rpy_control 1
#define mpu_auto_balance 2
#define gait_control 3

Servo *servo_arr = new Servo[12];
int servo_pin[12] = {2, 3, 4, 5, 6, 7, 8, 9, 10, 11, 12, 13};
int offset_arr[12] = {98, 166, 145, 68, 147, 84, 105, 28, 68, 72, -5, 110};//servo offset calibration
int init_arr[12] = {0, 135, 90, 0, 135, 90, 0, 135, 90, 0, 135, 90};//init servo angle
int write_arr[12];
int read_arr[12];

int leg_sensor_arr[4] = {0, 0, 0, 0};

float rpy[3] = {0, 0, 0};
float rpy_target[3] = { -0.02, 0, 0};
float rpy_limit[3] = {0.9, 0.6, 0.5};

float rpy_read[3];
float rpy_read_old[3];
float rpy_delta[3];

float rpy_k[3] = { -1.9, -1.9, 0};
float rpy_d[3] = { -0.055, -0.055, 0};

float rpy_f_k[3] = { 0, 0.4, 0};

float pos[3] = {2.3, 0, 9.5};
float leg_len[3] = {3, 6, 7.7};
//dog.body_ab_len = 3; dog.body_hip_len = 9;
//dog.foot_ab_len = 8; dog.foot_hip_len = 9;
body dog(3, 9, 12, 10, rpy, pos, leg_len);

float temp_v = 0;
int dir = 1;

float data_received[4] = {0}; //received control data

int overall_state;//general state

gait_generator generator(dog);

void setup() {
  Serial.begin(115200);

  generator.trot_delay = 70;
  generator.trot_height = 4.5;//set up generator;

  pinMode(A0, INPUT_PULLUP);
  pinMode(A1, INPUT_PULLUP);
  pinMode(A2, INPUT_PULLUP);
  pinMode(A3, INPUT_PULLUP);

  for (int s = 0; s < 12; s++)
    servo_arr[s].attach(servo_pin[s]);
  for (int s = 0; s < 12; s++)
    read_arr[s] = init_arr[s];

  mpu_init();
  FlexiTimer2::set(150, 1.0 / 1000, serial_read); // call every 150 1ms "ticks" to the serial reader
  FlexiTimer2::start();
}

void init_pos()
{
  servo_arr[0].write(98);//add clockwise FL
  servo_arr[1].write(170);//add clockwise
  servo_arr[2].write(142);//add clockwise

  servo_arr[3].write(68);//minus clockwise BL
  servo_arr[4].write(150);
  servo_arr[5].write(88);

  servo_arr[6].write(107);//add BR
  servo_arr[7].write(52);//minus
  servo_arr[8].write(68);//minus

  servo_arr[9].write(71);//minus
  servo_arr[10].write(0);//minus
  servo_arr[11].write(111);
}

void angle_trans(int *offset, int *read_arr, int *write_arr)
{
  write_arr[1] = read_arr[1] - 180 + offset[1];
  write_arr[4] = read_arr[4] - 180 + offset[4];

  write_arr[2] = read_arr[2] - 90 + offset[2];
  write_arr[5] = read_arr[5] - 90 + offset[5];

  write_arr[7] = 180 - read_arr[7] + offset[7];
  write_arr[10] = 180 - read_arr[10] + offset[10];

  write_arr[8] = 90 - read_arr[8] + offset[8];
  write_arr[11] = 90 - read_arr[11] + offset[11];

  write_arr[0] = offset[0] + read_arr[0];
  write_arr[3] = offset[3] - read_arr[3];
  write_arr[6] = offset[6] - (read_arr[6] + 180);
  write_arr[9] = offset[9] + read_arr[9] + 180;
}


void write_servo(int *data_write, int *offset)
{
  for (int s = 0; s < 12; s++)
  {
    servo_arr[s].write(data_write[s]);
  }
}

void print_leg_vec(body &in)
{
  Serial.print("fl: ");
  for (int s = 0; s < 3; s++) {
    Serial.print(in.leg_vec_fl.vec[s]);  Serial.print(" ");
  }
  Serial.println(" ");
  Serial.print("fr: ");
  for (int s = 0; s < 3; s++) {
    Serial.print(in.leg_vec_fr.vec[s]);  Serial.print(" ");
  }
  Serial.println(" ");
  Serial.print("bl: ");
  for (int s = 0; s < 3; s++) {
    Serial.print(in.leg_vec_bl.vec[s]);  Serial.print(" ");
  }
  Serial.println(" ");
  Serial.print("br: ");
  for (int s = 0; s < 3; s++) {
    Serial.print(in.leg_vec_br.vec[s]);  Serial.print(" ");
  }
  Serial.println(" ");

}

void print_angle(body &in)
{
  Serial.print("fl: ");
  Serial.print(in.fl.ab);  Serial.print(" ");
  Serial.print(in.fl.hip);  Serial.print(" ");
  Serial.print(in.fl.knee);  Serial.println(" ");
  Serial.print("fr: ");
  Serial.print(in.fr.ab);  Serial.print(" ");
  Serial.print(in.fr.hip);  Serial.print(" ");
  Serial.print(in.fr.knee);  Serial.println(" ");
  Serial.print("bl: ");
  Serial.print(in.bl.ab);  Serial.print(" ");
  Serial.print(in.bl.hip);  Serial.print(" ");
  Serial.print(in.bl.knee);  Serial.println(" ");
  Serial.print("br: ");
  Serial.print(in.br.ab);  Serial.print(" ");
  Serial.print(in.br.hip);  Serial.print(" ");
  Serial.print(in.br.knee);  Serial.println(" ");
}

void print_angle_write(int *arr)
{
  Serial.print("set: ");
  for (int s = 0; s < 12; s++)
  {
    Serial.print(arr[s]);
    Serial.print(" ");
  }
  Serial.println(" ");
}

void read_leg_sensor(int *arr)
{
  arr[0] = digitalRead(A0);
  arr[1] = digitalRead(A1);
  arr[2] = digitalRead(A2);
  arr[3] = digitalRead(A3);
}

void print_mpu_data(float *rpy_read)
{
  Serial.print(rpy_read[0]); Serial.print(",");
  Serial.print(rpy_read[1]); Serial.print(",");
  Serial.print(rpy_read[2]); Serial.println();
}

void serial_read()
{
  if (Serial.available())
  {
    if (Serial.read() == 'h')
      for (int i = 0; i < 4; i++)
        *(data_received + i) = Serial.parseFloat();
  }
  if (int(data_received[0]) != overall_state)
    overall_state = data_received[0];//change main state
}

void loop() {

  read_leg_sensor(leg_sensor_arr);
  mpu_update(rpy_read);
  //serial_read();

  //if (!(leg_sensor_arr[0] == SKY && leg_sensor_arr[1] == SKY && leg_sensor_arr[2] == SKY && leg_sensor_arr[3] == SKY))
  /*for (int s = 0; s < 2; s++)
    {
    rpy_delta[s] = rpy_read[s] - rpy_target[s];
    rpy[s] += (rpy_k[s] * rpy_delta[s] * abs(rpy_delta[s]) + rpy_d[s] * (rpy_read[s] - rpy_read_old[s]));

    rpy_read_old[s] = rpy_read[s];

    if (rpy[s] > rpy_limit[s]) rpy[s] = rpy_limit[s];
    else if (rpy[s] < -1 * rpy_limit[s]) rpy[s] = -1 * rpy_limit[s];
    }*/

  //dog.change_dog_pos(rpy, pos);
  //Serial.print("time interval a  ");
  //Serial.print(generator.atime_ground_s);
  //Serial.print("   time interval b  ");
  //Serial.println(generator.btime_ground_s);

  if (generator.main_state == -1)
  {
    if (!(leg_sensor_arr[0] == SKY && leg_sensor_arr[1] == SKY && leg_sensor_arr[2] == SKY && leg_sensor_arr[3] == SKY))
      generator.main_state = LOADING_A;
  }

  float vec_x = data_received[1];
  float vec_y = data_received[2];
  float vec_turn = data_received[3];
  generator.trot_changer(dog, leg_sensor_arr, rpy, pos, vec_x, vec_y, vec_turn, rpy_read, rpy_target, rpy_f_k);

  read_arr[0] = dog.fl.ab;   read_arr[1] = dog.fl.hip;    read_arr[2] = dog.fl.knee;
  read_arr[3] = dog.bl.ab;   read_arr[4] = dog.bl.hip;    read_arr[5] = dog.bl.knee;
  read_arr[6] = dog.br.ab;   read_arr[7] = dog.br.hip;    read_arr[8] = dog.br.knee;
  read_arr[9] = dog.fr.ab;   read_arr[10] = dog.fr.hip;    read_arr[11] = dog.fr.knee;

  angle_trans(offset_arr, read_arr, write_arr);

  write_servo(write_arr, offset_arr);

  //Serial.print("state ");
  //Serial.println(generator.main_state);

  //fl,bl,br,fr cycle
}

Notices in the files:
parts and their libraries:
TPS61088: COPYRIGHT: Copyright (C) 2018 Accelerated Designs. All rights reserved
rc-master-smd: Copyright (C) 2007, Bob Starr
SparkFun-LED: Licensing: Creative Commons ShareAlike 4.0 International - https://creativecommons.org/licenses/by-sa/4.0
